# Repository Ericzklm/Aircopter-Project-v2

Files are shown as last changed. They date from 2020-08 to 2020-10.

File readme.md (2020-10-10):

# Aircopter Project

This project was done in association with the IEEE Student Branch on the UCLA campus.
This is the second iteration of the project. Due to the 2020 global pandemic, this
project was cut short for the 2019-2020 academic year and will resume in the 2020-
2021 academic year.

The goal of the project was to: 1. Design and assemble a custom PCB for a drone,
2. Write a program to hover the drone, then fly the drone. Because of the nature
of the project, the PCB was required to be small and compact (meaning SMD soldering
was needed) and the program needed to be quick and responsive.

#### Note: 

This version of the project was cut short due to the 2020 pandemic. The code was still
written and the board was still designed and printed but we were not able to assemble
and solder the final product because we were then living off-campus and all campus
activities we're mandated to be put on hold.

### Hardware Selection Choices:

**MCU**: The main chip is the model STM32F405. This was chosen for its ideal balance
between size and functionality. It is able to support all the needed sensors and
motor drivers for our drone and can be powered by a 3.3v supply which closely
matches the 3.7v of standard drone batteries (3.7v is stepped down to 3.3 using
a voltage regulator). Additionally, this chip was more ideal than other chips of
similar style because it handles floating point calculations better which allows
for simplicity and efficiency when writing the program.

**Voltage Regulator**: The voltage regulator used is the LTC3246MPMSE from Linear 
Technology. This component was chosen since it is a buck boost regulator with
the ability to step down or step up voltage as we need in this application. This
component is larger, more expensive, and more complex than the regulator used in
the first iteration but it accomplishes the same purpose while being much easier
to solder onto the board (no heat guns required).

**Wireless Module**: The wireless module used is the nrf24l01 which is standard, easy
to use, and familiar so we used it in this application since it fits well with the
acclerometer module.

**Accelerometer/Gyroscope**: The module used is the mpu6050 which is standard, easy to
use, and familiar so we used it in this application since it fits well with the
wireless module.

**Oscillator**: We opted for an abracon 25mhz crystal oscillator. The frequency fits 
the range of our operation and takes up a relatively small amount of space on
the PCB. In this iteration, a through-hole component was chosen because it could
be added more compactly without needing large pads on the PCB outside the area of
the oscillator.

**Passive Components**: For the resistors, capacitors, and inductors, we primarily
used parts with the package size 0603 which would fit the board without being
overly difficult to solder. Each piece was checked for its operating voltages as 
well as the operating temperatures to make sure no issues would arise. Additonally,
we tried to get components that were less dependent on external passive components
so we could make the PCB more compact/efficient.

### Hardware Design Choices:

**Motors**: In this design, we opted to place the 4 motor JST connectors along the left
side of the board because this would reduce the amount of "prime-real-estate" occupied
by the motor drivers. Also, we saved a significant amount of space on the PCB by
moving the motor drivers to the backside, under the JST rather than having the drivers
being on the same side (which means we cannot overlap the area occupied by the JSTs).

**Battery**: The JST of the battery is placed directly right of the motors. This is
important since its a central component and that position allows it easy access to
the motors and the rest of the PCB.

**Voltage Regulator**: The voltage regulator is placed below the battery JST, also in a
central position. This is key because we are able to define the 3.7V and 3.3V polygons
without complexity, and therefore reduing bottlenecks. Because the voltage regulator
is dependent on several passive components, it is placed in an open space with the
passive components compactly fit around it, without creating any major bottlenecks.

**Polygons**: Because of the location of the voltage divider, we are able to make an easy
distinction between the 3.3v, 3.7v, motor ground, and general ground planes. Everything
left of the voltage regulator is either the 3.7v or motor ground planes while everything
right is either 3.3v or general ground.

**MCU**: We chose to turn the MCU 45 degrees for a few reasons:
  1. Having the MCU turned actually signficantly reduced the bottlenecks as key 
  components had more direct access to the 3.3v plane and we had less "dead-ends" in 
  the plane. This gave extra space to work in that would not present a threat of 
  bottlenecking.
  2. The traces coming out of the MCU can be shorter and more optimized for the key
  components.
  3. We thought it looked neat!

**Oscillator**: The oscillator is placed as physically close to the MCU as possible with
relatively thick traces in order to prevent that signal from being overly distorted.

**Wireless Module/Accelerometer**: Because these two modules are not raised to the same
level, they can be overlapping on the PCB and not cause any issues. The wireless
module is placed along the right side while the accelerometer is placed along the
bottom because this allows for easy access to the respective connections on the MCU.

**Other items**: This includes the programmer and the reset switch. Since neither of them
are crucial in the operation of the drone, they are place along the top with less
direct connections (meaning the traces and planes for key components are better
optimized). Additionally, this iteration includes a tx and rx connection which will
be useful for debugging.

**Bottlenecks**: For this version, we were able to get away with no major bottlenecks
in the planes thanks to the reduction of passive components, better placements,
and the 45 degree MCU.

**Decoupling Capacitors**: The decoupling capacitors are placed in such a way that they
are close to the components they stabalize. This also helped in reducing bottlenecks
as passive components were not cutting up the planes

### Possible Improvements:

Some components are not optimally placed meaning the traces are not direct. This can
be solved by either tweaking the placement or choosing different compatible pins on
the MCU. Also the placement of the motors and battery mean that the lower motors are
further away from the power source, meaning potentially higher noise. Furthermore,
adding some LEDs would be useful for debugging (we have the room to do so).

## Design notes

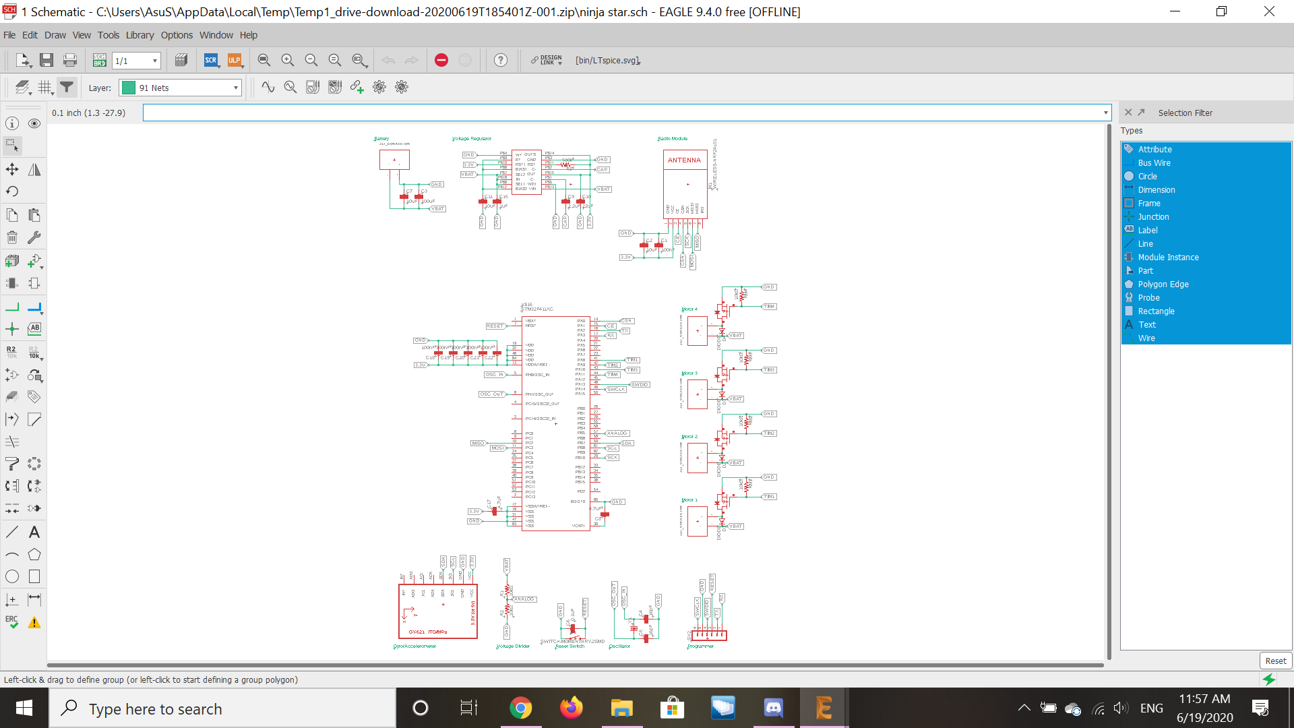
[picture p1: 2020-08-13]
Hardware/Schematic1.png

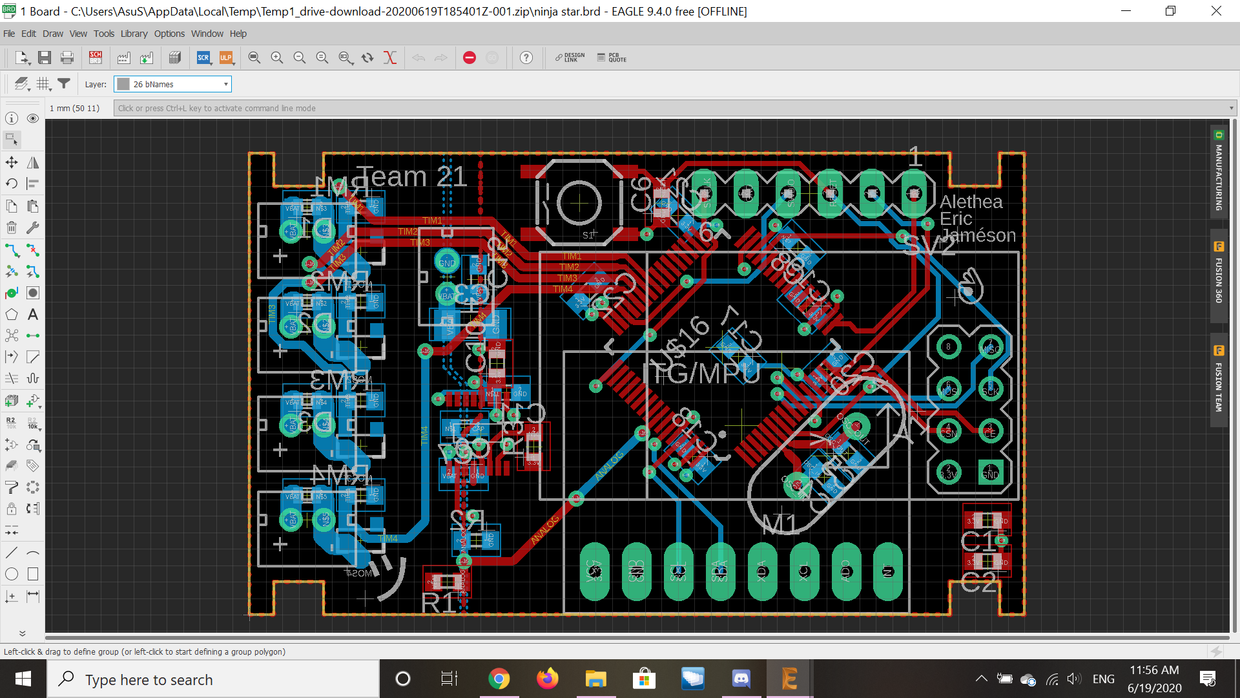
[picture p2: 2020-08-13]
Hardware/PCB2.png

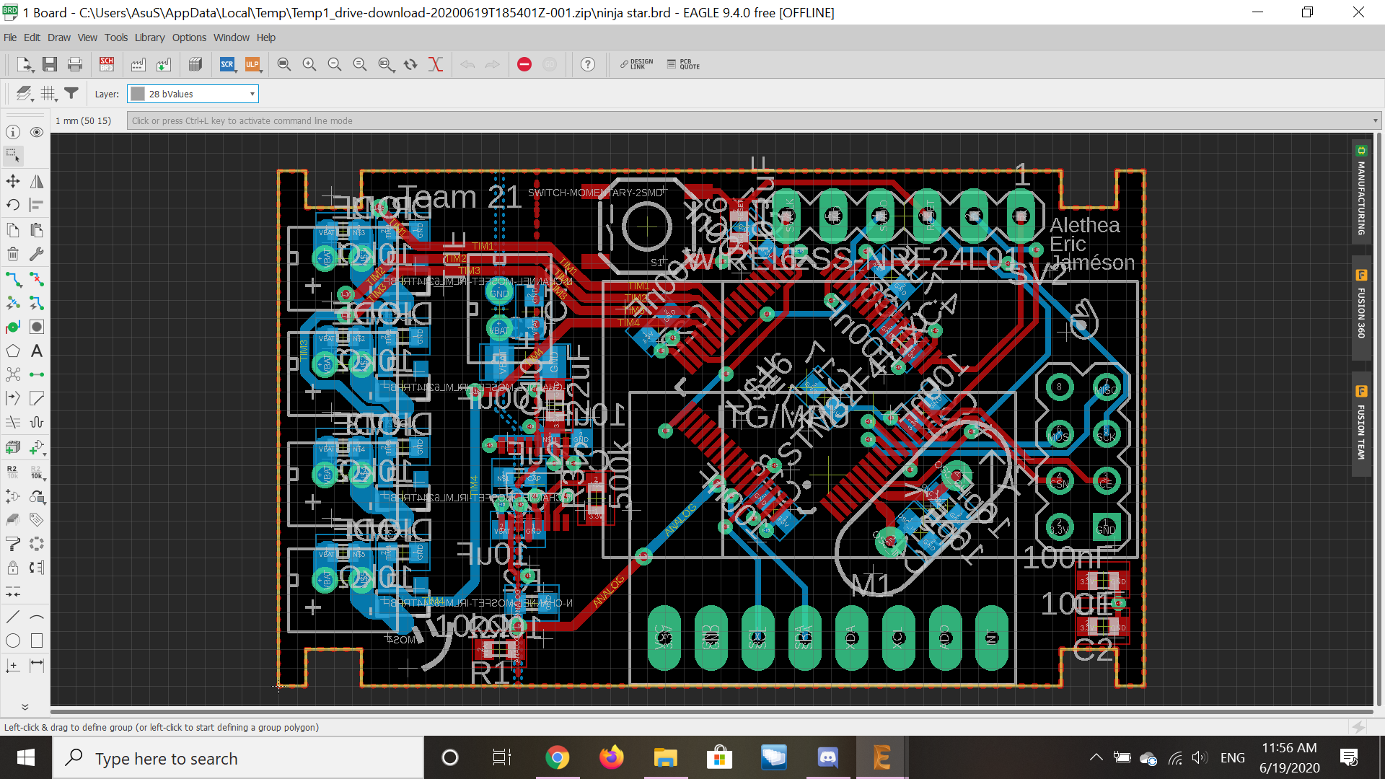
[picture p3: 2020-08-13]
Hardware/PCB4.png

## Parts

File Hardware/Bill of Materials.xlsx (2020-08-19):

Vendor | Vendor Part # | Manufacturer | Part # | Package | Description | Quantity | Unit Price | 65.65 | Link | Datasheet
Mouser | 511-STM32F411CEU6TR | STMicroelectronics | STM32F411CEU6TR | yes | ARM Microcontrollers - MCU High-performance access line, ARM Cortex-M4 core with DSP and FPU, 512 Kbytes Flash, 100 MHz CPU, ART Accelerator | 1 | $5.56 | $5.56 | https://www.mouser.com/ProductDetail/STMicroelectronics/STM32F411CEU6TR | https://www.mouser.com/datasheet/2/389/stm32f411ce-956237.pdf
Mouser | LTC3246MPMSE#PBF | Analog Devices/Linear Technology | TPS63805YFFR | DSBGA-15 | Voltage Regulator | 1 | $15.00 | $15.00 | https://www.mouser.com/ProductDetail/Analog-Devices-Linear-Technology/LTC3246MPMSEPBF | https://www.mouser.com/datasheet/2/609/3246fa-1275517.pdf
Digi-Key | 535-13438-1-ND | Ablacon LC | ABLS2-25.000MHZ-2X-FT | HC-49/US | Crystal Oscillator | 1 | $0.46 | $0.46 | https://www.digikey.com/product-detail/en/abracon-llc/ABLS2-25.000MHZ-2X-FT/535-13438-1-ND/5980114
Digi-Key | GH7585DKR-ND | Grayhill Inc. | 14AP-L1-02-G | Digi-Reel | Pushbutton | 1 | $4.64 | $4.64 | https://www.digikey.com/product-detail/en/grayhill-inc/14AP-L1-02-G/GH7585DKR-ND/5357261
Mouser | 652-CD0603-S01575 | Bourns | CD0603-S01575 | 0603 | Diode | 4 | $0.39 | $1.56 | https://www.mouser.com/ProductDetail/Bourns/CD0603-S01575?qs=FITO%2f%2fQgYDlmbwJLjhqThQ%3d%3d
Mouser | 942-IRLML6244TRPBF | Infineon Technologies | IRLML6244TRPBF | SOT-23-3 | NMOS MOSFET MOSFT 20V 6.3A 21mOhm 2.5V cpbl | 4 | $0.37 | $1.48 | http://www.mouser.com/Search/ProductDetail.aspx | https://www.mouser.com/datasheet/2/196/irlml6244pbf-1228275.pdf
Digi-Key | 490-10525-1-ND | Murata Electronics | GRM31CD80J107ME39L | 1206 | CAP CER 100UF 6.3V X6T 1206 | 1 | $0.76 | $0.76 | https://www.digikey.com/product-detail/en/murata-electronics/GRM31CD80J107ME39L/490-10525-1-ND/5026461 | https://search.murata.co.jp/Ceramy/image/img/A01X/G101/ENG/GRM31CD80J107ME39-01.pdf
Digi-Key | 490-12538-1-ND | Murata Electronics | GRM188R60J106KE47D | 0603 | CAP CER 10UF 6.3V X5R 0603 | 3 | $0.19 | $0.57 | https://www.digikey.com/product-detail/en/murata-electronics/GRM188R60J106KE47D/490-12538-1-ND/5797528 | https://search.murata.co.jp/Ceramy/image/img/A01X/G101/ENG/GRM188R60J106KE47-02.pdf
Digi-Key | 490-12738-1-ND | Murata Electronics | GRM188R61E225MA12D | 0603 | CAP CER 2.2UF 25V X5R 0603 | 1 | $0.16 | $0.16 | https://www.digikey.com/product-detail/en/murata-electronics/GRM188R61E225MA12D/490-12738-1-ND/5797707 | https://search.murata.co.jp/Ceramy/image/img/A01X/G101/ENG/GRM188R61E225MA12-01.pdf
Digi-Key | CL10F104ZO8NNNC | Samsung Electro-Mechanics | 1276-1258-1-ND | 0603 | CAP CER 0.1UF 16V Y5V 0603 | 7 | $0.10 | $0.70 | https://www.digikey.com/product-detail/en/samsung-electro-mechanics/CL10F104ZO8NNNC/1276-1258-1-ND/3889344 | http://www.samsungsem.com/kr/support/product-search/mlcc/CL10F104ZO8NNNC.jsp
Digi-Key | 1276-2204-1-ND | Samsung Electro-Mechanics | CL10C160JB8NNNC | 0603 | CAP CER 16PF 50V C0G/NP0 0603 | 2 | $0.10 | $0.20 | https://www.digikey.com/product-detail/en/samsung-electro-mechanics/CL10C160JB8NNNC/1276-2204-1-ND/3890290 | http://www.samsungsem.com/kr/support/product-search/mlcc/__icsFiles/afieldfile/2018/06/11/CL10C160JB8NNNC.pdf
Digi-Key | 1276-6524-1-ND | Samsung Electro-Mechanics (http://www.samsungsem.com/global/index.jsp) | CL10B105MO8NNWC | 0603 | CAP CER 1UF 16V X7R 0603 | 1 | $0.10 | $0.10 | https://www.digikey.com/product-detail/en/samsung-electro-mechanics/CL10B105MO8NNWC/1276-6524-1-ND/5961383 | http://www.samsungsem.com/kr/support/product-search/mlcc/__icsFiles/afieldfile/2018/07/24/CL10B105MO8NNWC.pdf
Digi-Key | 1276-2868-1-ND | Samsung Electro-Mechanics | CL10A226MQ8NRNE | 0603 | CAP CER 22UF 6.3V X5R 0603 | 1 | $0.34 | $0.34 | https://www.digikey.com/product-detail/en/samsung-electro-mechanics/CL10A226MQ8NRNE/1276-2868-1-ND/3890954 | http://www.samsungsem.com/kr/support/product-search/mlcc/__icsFiles/afieldfile/2018/06/20/CL10A226MQ8NRNE.pdf
Digi-Key | 311-1820-1-ND | Yageo | CC0603MRX5R6BB475 | 0603 | CAP CER 4.7UF 10V X5R 0603 | 2 | $0.21 | $0.42 | https://www.digikey.com/product-detail/en/yageo/CC0603MRX5R6BB475/311-1820-1-ND/5195722 | https://www.yageo.com/upload/media/product/productsearch/datasheet/mlcc/UPY-GPHC_X5R_4V-to-50V_25.pdf
Digi-Key | 311-10KGRCT-ND | Yageo | RC0603JR-0710KL | 0603 | RES SMD 10K OHM 5% 1/10W 0603 | 6 | $0.10 | $0.60 | https://www.digikey.com/product-detail/en/yageo/RC0603JR-0710KL/311-10KGRCT-ND/729647 | https://www.yageo.com/upload/media/product/productsearch/datasheet/rchip/PYu-RC_Group_51_RoHS_L_10.pdf
Digi-Key | 749-1661-1-ND | Vishay Beyschlag | MCT06030C4993FP500 | 0603 | RES SMD 499K OHM 1% 1/8W 0603 | 1 | $0.17 | $0.17 | https://www.digikey.com/product-detail/en/vishay-beyschlag/MCT06030C4993FP500/749-1661-1-ND/7347969 | http://www.vishay.com/docs/28705/mcx0x0xpro.pdf
 |  |  |  |  |  |  |  | 0
 |  |  |  |  |  |  |  | 0
 |  |  |  |  |  |  |  | 0
 |  |  |  |  |  |  |  | 0
 |  |  |  |  |  |  |  | 0
 |  |  |  |  |  |  |  | 0
 |  |  |  |  |  |  |  | 0
 |  |  |  |  |  |  |  | 0
 |  |  |  |  |  |  |  | 0
 |  |  |  |  |  |  |  | 0

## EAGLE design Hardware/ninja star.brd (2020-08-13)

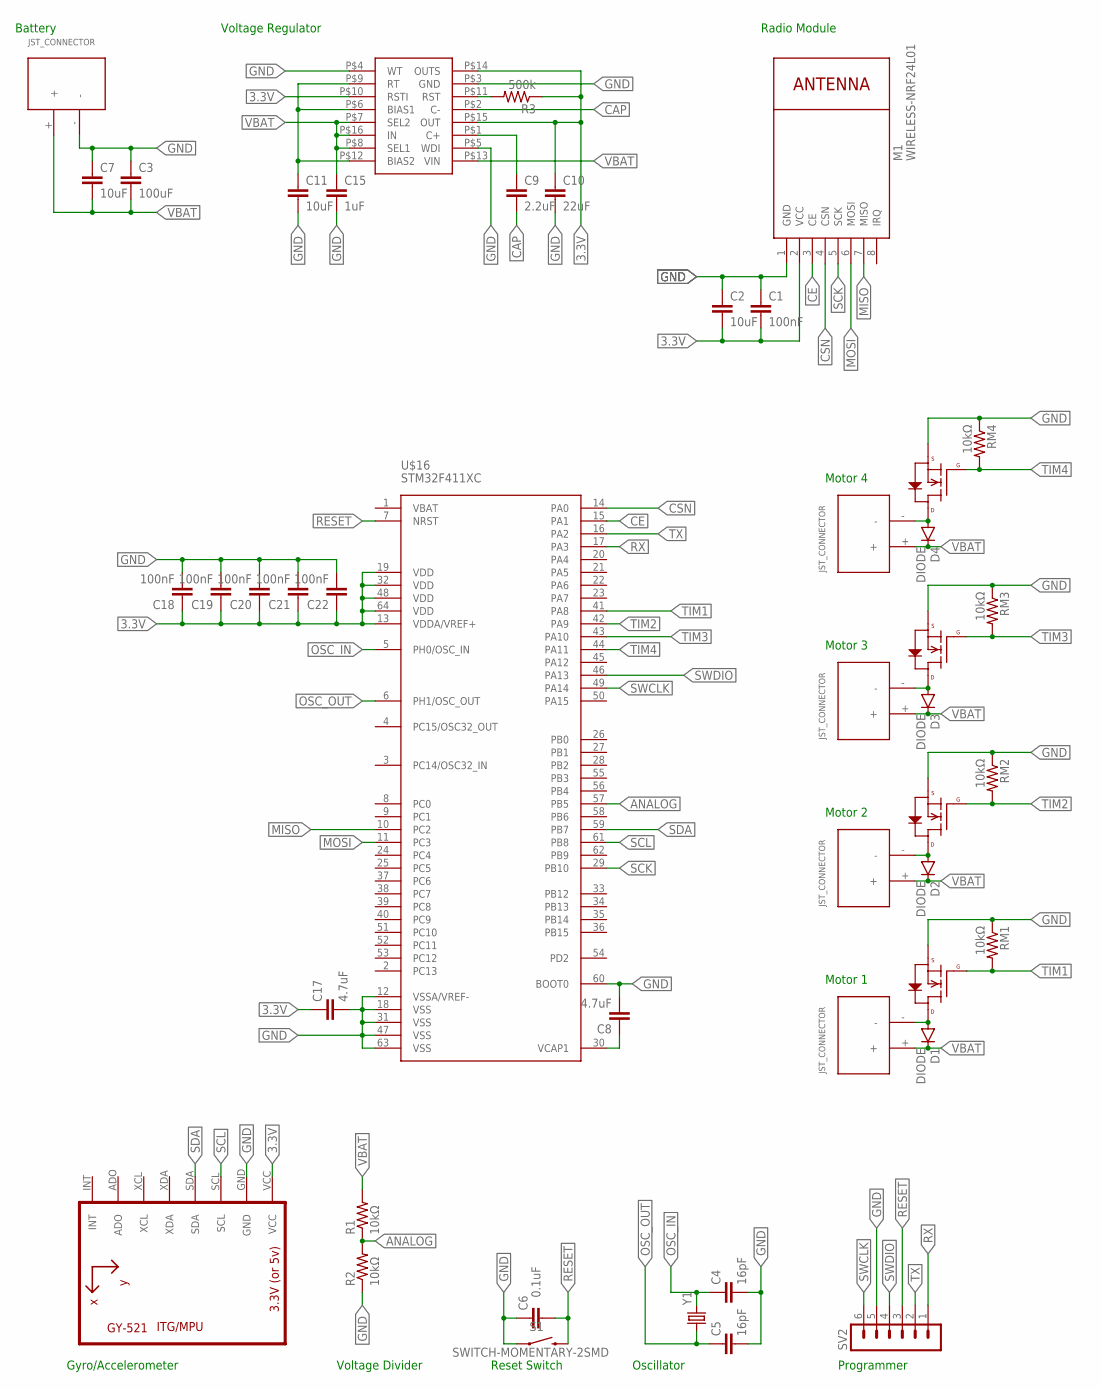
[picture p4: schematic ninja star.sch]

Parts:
C1, C18, C19, C20, C21, C22: 100nF; C0603
C2, C7, C11: 10uF; C0603
C3: 100uF; C1206
C4, C5: 16pF; C0603
C6: 0.1uF; C0603
C8, C17: 4.7uF; C0603
C9: 2.2uF; C0603
C10: 22uF; C0603
C15: 1uF; C0603
D1, D2, D3, D4: DIODE; C0603
M1: WIRELESS-NRF24L01
MOS1, MOS2, MOS3, MOS4: N-CHANNEL-MOSFET-IRLML6244TRPBF; SOT23-3
MOTOR1, MOTOR2, MOTOR3, MOTOR4: JST_CONNECTOR_FEMALE
R1, R2: 10kΩ; R0603
R3: 500k; R0603
RM1, RM2, RM3, RM4: 10kΩ; R0603
S1: SWITCH-MOMENTARY-2SMD; TACTILE-SWITCH-SMD
SV2: MA06-1
U1: GY-521MPU6050; GY-521
U$7: JST_CONNECTOR_FEMALE
U$12: VR-LTC3246; MSOP-16
U$16: STM32F411XC; LQFP64
Y1: CRYSTALHC49US; HC49US

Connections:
3.3V: C1.2, C2.2, C10.1, C17.1, C18.1, C19.1, C20.1, C21.1, C22.1, M1.2 (VCC), R3.1, U1.VCC, U$12.P$10 (RSTI), U$12.P$14 (OUTS), U$12.P$15 (OUT), U$16.13 (VDDA/VREF+), U$16.19 (VDD), U$16.32 (VDD), U$16.48 (VDD), U$16.64 (VDD)
ANALOG: R1.1, R2.2, U$16.57 (PB5)
CAP: C9.2, U$12.P$2 (C-)
CE: M1.3 (CE), U$16.15 (PA1)
CSN: M1.4 (CSN), U$16.14 (PA0)
GND: C1.1, C2.1, C3.1, C4.2, C5.2, C6.1, C7.1, C8.2, C10.2, C11.2, C15.2, C17.2, C18.2, C19.2, C20.2, C21.2, C22.2, M1.1 (GND), MOS1.2 (S), MOS2.2 (S), MOS3.2 (S), MOS4.2 (S), R2.1, RM1.1, RM2.1, RM3.1, RM4.1, S1.1, SV2.5, U1.GND, U$7.-, U$12.P$3 (GND), U$12.P$4 (WT), U$12.P$5 (WDI), U$16.12 (VSSA/VREF-), U$16.18 (VSS), U$16.31 (VSS), U$16.47 (VSS), U$16.60 (BOOT0), U$16.63 (VSS)
MISO: M1.7 (MISO), U$16.10 (PC2)
MOSI: M1.6 (MOSI), U$16.11 (PC3)
unnamed: C9.1, U$12.P$1 (C+)
unnamed: D2.2 (PPIN), MOS2.3 (D), MOTOR2.-
unnamed: D1.2 (PPIN), MOS1.3 (D), MOTOR1.-
unnamed: D3.2 (PPIN), MOS3.3 (D), MOTOR3.-
unnamed: D4.2 (PPIN), MOS4.3 (D), MOTOR4.-
unnamed: R3.2, U$12.P$11 (RST)
unnamed: C8.1, U$16.30 (VCAP1)
unnamed: C11.1, U$12.P$6 (BIAS1), U$12.P$9 (RT), U$12.P$12 (BIAS2)
OSC_IN: C4.1, U$16.5 (PH0/OSC_IN), Y1.2
OSC_OUT: C5.1, U$16.6 (PH1/OSC_OUT), Y1.1
RESET: C6.2, S1.3 (2), SV2.3, U$16.7 (NRST)
RX: SV2.1, U$16.17 (PA3)
SCK: M1.5 (SCK), U$16.29 (PB10)
SCL: U1.SCL, U$16.61 (PB8)
SDA: U1.SDA, U$16.59 (PB7)
SWCLK: SV2.6, U$16.49 (PA14)
SWDIO: SV2.4, U$16.46 (PA13)
TIM1: MOS1.1 (G), RM1.2, U$16.41 (PA8)
TIM2: MOS2.1 (G), RM2.2, U$16.42 (PA9)
TIM3: MOS3.1 (G), RM3.2, U$16.43 (PA10)
TIM4: MOS4.1 (G), RM4.2, U$16.44 (PA11)
TX: SV2.2, U$16.16 (PA2)
VBAT: C3.2, C7.2, C15.1, D1.1 (GPIN), D2.1 (GPIN), D3.1 (GPIN), D4.1 (GPIN), MOTOR1.+, MOTOR2.+, MOTOR3.+, MOTOR4.+, R1.2, U$7.+, U$12.P$7 (SEL2), U$12.P$8 (SEL1), U$12.P$13 (VIN), U$12.P$16 (IN)

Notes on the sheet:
Battery
Voltage Divider
Voltage Regulator
Radio Module
Motor 4
Motor 3
Motor 2
Motor 1
Gyro/Accelerometer
Reset Switch
Oscillator
Programmer

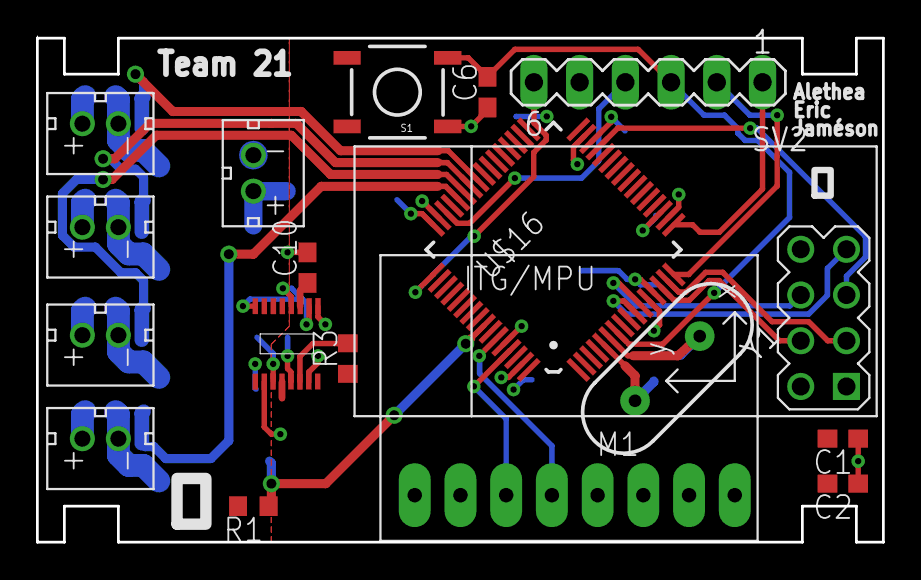
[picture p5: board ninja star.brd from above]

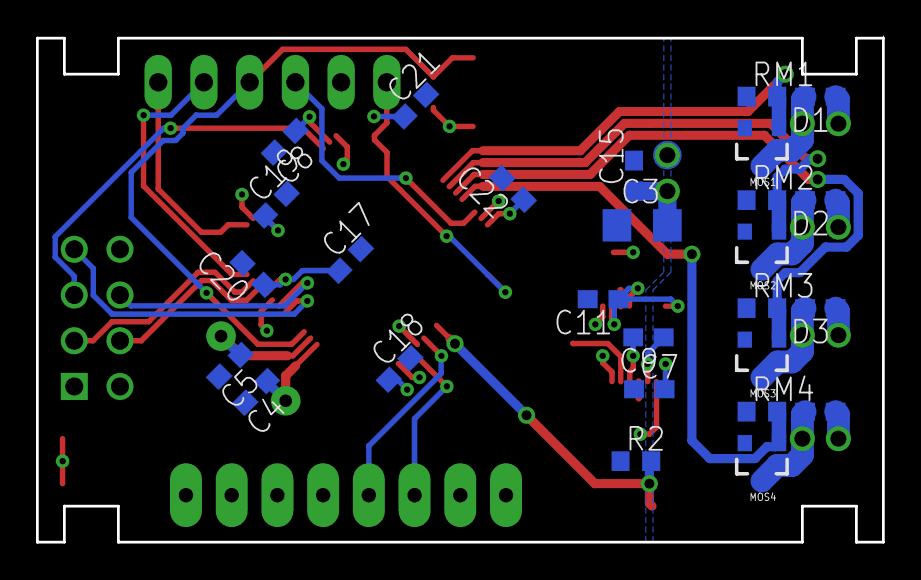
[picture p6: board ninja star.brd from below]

Board: 2 copper layers, 47.0 x 28.0 mm, 45 parts (27 on the bottom side), 31 nets.

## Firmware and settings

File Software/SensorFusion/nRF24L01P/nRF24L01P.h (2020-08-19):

#ifndef __NRF24L01P_H__
#define __NRF24L01P_H__

/**
 * Includes
 */
#include "mbed.h"

/**
 * Defines
 */
#define NRF24L01P_TX_PWR_ZERO_DB         0
#define NRF24L01P_TX_PWR_MINUS_6_DB     -6
#define NRF24L01P_TX_PWR_MINUS_12_DB   -12
#define NRF24L01P_TX_PWR_MINUS_18_DB   -18

#define NRF24L01P_DATARATE_250_KBPS    250
#define NRF24L01P_DATARATE_1_MBPS     1000
#define NRF24L01P_DATARATE_2_MBPS     2000

#define NRF24L01P_CRC_NONE               0
#define NRF24L01P_CRC_8_BIT              8
#define NRF24L01P_CRC_16_BIT            16

#define NRF24L01P_MIN_RF_FREQUENCY    2400
#define NRF24L01P_MAX_RF_FREQUENCY    2525

#define NRF24L01P_PIPE_P0                0
#define NRF24L01P_PIPE_P1                1
#define NRF24L01P_PIPE_P2                2
#define NRF24L01P_PIPE_P3                3
#define NRF24L01P_PIPE_P4                4
#define NRF24L01P_PIPE_P5                5

/**
* Default setup for the nRF24L01+, based on the Sparkfun "Nordic Serial Interface Board"
*  for evaluation (http://www.sparkfun.com/products/9019)
*/
#define DEFAULT_NRF24L01P_ADDRESS       ((unsigned long long) 0xE7E7E7E7E7 )
#define DEFAULT_NRF24L01P_ADDRESS_WIDTH  5
#define DEFAULT_NRF24L01P_CRC            NRF24L01P_CRC_8_BIT
#define DEFAULT_NRF24L01P_RF_FREQUENCY  (NRF24L01P_MIN_RF_FREQUENCY + 2)
#define DEFAULT_NRF24L01P_DATARATE       NRF24L01P_DATARATE_1_MBPS
#define DEFAULT_NRF24L01P_TX_PWR         NRF24L01P_TX_PWR_ZERO_DB
#define DEFAULT_NRF24L01P_TRANSFER_SIZE  4

/**
 * nRF24L01+ Single Chip 2.4GHz Transceiver from Nordic Semiconductor.
 */
class nRF24L01P {

public:

    /**
     * Constructor.
     *
     * @param mosi mbed pin to use for MOSI line of SPI interface.
     * @param miso mbed pin to use for MISO line of SPI interface.
     * @param sck mbed pin to use for SCK line of SPI interface.
     * @param csn mbed pin to use for not chip select line of SPI interface.
     * @param ce mbed pin to use for the chip line.
     * @param irq mbed pin to use for the interrupt request line.
     */
    nRF24L01P(PinName mosi, PinName miso, PinName sck, PinName csn, PinName ce, PinName irq = NC);

    /**
     * Set the RF frequency.
     *
     * @param frequency the frequency of RF transmission in MHz (2400..2525).
     */
    void setRfFrequency(int frequency = DEFAULT_NRF24L01P_RF_FREQUENCY);

    /**
     * Get the RF frequency.
     *
     * @return the frequency of RF transmission in MHz (2400..2525).
     */
    int getRfFrequency(void);

    /**
     * Set the RF output power.
     *
     * @param power the RF output power in dBm (0, -6, -12 or -18).
     */
    void setRfOutputPower(int power = DEFAULT_NRF24L01P_TX_PWR);

    /**
     * Get the RF output power.
     *
     * @return the RF output power in dBm (0, -6, -12 or -18).
     */
    int getRfOutputPower(void);

    /**
     * Set the Air data rate.
     *
     * @param rate the air data rate in kbps (250, 1M or 2M).
     */
    void setAirDataRate(int rate = DEFAULT_NRF24L01P_DATARATE);

    /**
     * Get the Air data rate.
     *
     * @return the air data rate in kbps (250, 1M or 2M).
     */
    int getAirDataRate(void);

    /**
     * Set the CRC width.
     *
     * @param width the number of bits for the CRC (0, 8 or 16).
     */
    void setCrcWidth(int width = DEFAULT_NRF24L01P_CRC);

    /**
     * Get the CRC width.
     *
     * @return the number of bits for the CRC (0, 8 or 16).
     */
    int getCrcWidth(void);

    /**
     * Set the Receive address.
     *
     * @param address address associated with the particular pipe
     * @param width width of the address in bytes (3..5)
     * @param pipe pipe to associate the address with (0..5, default 0)
     *
     * Note that Pipes 0 & 1 have 3, 4 or 5 byte addresses,
     *  while Pipes 2..5 only use the lowest byte (bits 7..0) of the
     *  address provided here, and use 2, 3 or 4 bytes from Pipe 1's address.
     *  The width parameter is ignored for Pipes 2..5.
     */
    void setRxAddress(unsigned long long address = DEFAULT_NRF24L01P_ADDRESS, int width = DEFAULT_NRF24L01P_ADDRESS_WIDTH, int pipe = NRF24L01P_PIPE_P0);

    void setRxAddress(unsigned long msb_address, unsigned long lsb_address, int width, int pipe = NRF24L01P_PIPE_P0);

    /**
     * Set the Transmit address.
     *
     * @param address address for transmission
     * @param width width of the address in bytes (3..5)
     *
     * Note that the address width is shared with the Receive pipes,
     *  so a change to that address width affect transmissions.
     */
    void setTxAddress(unsigned long long address = DEFAULT_NRF24L01P_ADDRESS, int width = DEFAULT_NRF24L01P_ADDRESS_WIDTH);

    void setTxAddress(unsigned long msb_address, unsigned long lsb_address, int width);

    /**
     * Get the Receive address.
     *
     * @param pipe pipe to get the address from (0..5, default 0)
     * @return the address associated with the particular pipe
     */
    unsigned long long getRxAddress(int pipe = NRF24L01P_PIPE_P0);

    /**
     * Get the Transmit address.
     *
     * @return address address for transmission
     */
    unsigned long long getTxAddress(void);

    /**
     * Set the transfer size.
     *
     * @param size the size of the transfer, in bytes (1..32)
     * @param pipe pipe for the transfer (0..5, default 0)
     */
    void setTransferSize(int size = DEFAULT_NRF24L01P_TRANSFER_SIZE, int pipe = NRF24L01P_PIPE_P0);

    /**
     * Get the transfer size.
     *
     * @return the size of the transfer, in bytes (1..32).
     */
    int getTransferSize(int pipe = NRF24L01P_PIPE_P0);


    /**
     * Get the RPD (Received Power Detector) state.
     *
     * @return true if the received power exceeded -64dBm
     */
    bool getRPD(void);

    /**
     * Put the nRF24L01+ into Receive mode
     */
    void setReceiveMode(void);

    /**
     * Put the nRF24L01+ into Transmit mode
     */
    void setTransmitMode(void);

    /**
     * Power up the nRF24L01+ into Standby mode
     */
    void powerUp(void);

    /**
     * Power down the nRF24L01+ into Power Down mode
     */
    void powerDown(void);

    /**
     * Enable the nRF24L01+ to Receive or Transmit (using the CE pin)
     */
    void enable(void);

    /**
     * Disable the nRF24L01+ to Receive or Transmit (using the CE pin)
     */
    void disable(void);

    /**
     * Transmit data
     *
     * @param pipe is ignored (included for consistency with file write routine)
     * @param data pointer to an array of bytes to write
     * @param count the number of bytes to send (1..32)
     * @return the number of bytes actually written, or -1 for an error
     */
    int write(int pipe, char *data, int count);
    
    /**
     * Receive data
     *
     * @param pipe the receive pipe to get data from
     * @param data pointer to an array of bytes to store the received data
     * @param count the number of bytes to receive (1..32)
     * @return the number of bytes actually received, 0 if none are received, or -1 for an error
     */
    int read(int pipe, char *data, int count);

    /**
     * Determine if there is data available to read
     *
     * @param pipe the receive pipe to check for data
     * @return true if the is data waiting in the given pipe
     */
    bool readable(int pipe = NRF24L01P_PIPE_P0);

    /**
     * Disable all receive pipes
     *
     * Note: receive pipes are enabled when their address is set.
     */
    void disableAllRxPipes(void);
    
    /**
     * Disable AutoAcknowledge function
     */
    void disableAutoAcknowledge(void);
    
    /**
     * Enable AutoAcknowledge function
     *
     * @param pipe the receive pipe
     */
    void enableAutoAcknowledge(int pipe = NRF24L01P_PIPE_P0);
    
    /**
     * Disable AutoRetransmit function
     */
    void disableAutoRetransmit(void);
    
    /**
     * Enable AutoRetransmit function
     *
     * @param delay the delay between restransmits, in uS (250uS..4000uS)
     * @param count number of retransmits before generating an error (1..15)
     */
    void enableAutoRetransmit(int delay, int count);

private:

    /**
     * Get the contents of an addressable register.
     *
     * @param regAddress address of the register
     * @return the contents of the register
     */
    int getRegister(int regAddress);

    /**
     * Set the contents of an addressable register.
     *
     * @param regAddress address of the register
     * @param regData data to write to the register
     */
    void setRegister(int regAddress, int regData);

    /**
     * Get the contents of the status register.
     *
     * @return the contents of the status register
     */
    int getStatusRegister(void);

    SPI         spi_;
    DigitalOut  nCS_;
    DigitalOut  ce_;
    InterruptIn nIRQ_;

    int mode;

};

#endif /* __NRF24L01P_H__ */

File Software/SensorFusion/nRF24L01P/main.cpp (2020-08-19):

#include "mbed.h"
#include "sensor_fusion.h"
#include "quaternion.h"
#include "millis.h"



MPU6050 MPU(D4,D5);
Serial pc(USBTX, USBRX); //create a Serial object
Timer timer;

int main() {
    MPU.start();
    timer.start();
    pc.baud(115200);
    float t;
    float mag;
    float pi = 3.14159265358979;
    int i=0;
    float sumgx,sumgy,sumgz,sumax,sumay,sumaz;
    float biasgx,biasgy,biasgz,biasax,biasay,biasaz;
    float gx,gy,gz,ax,ay,az;
    
    vector n;
    n.x=0;
    n.y=0;
    n.z=1;
    
    vector pointv;
    pointv.x=0;
    pointv.y=0;
    pointv.z=1;
    
    
    while(i<=19) 
    {
            
        if (MPU.data_ready() == 1) 
        {
            MPU.read_raw(&gx,&gy,&gz,&ax,&ay,&az);
            sumgx+=gx;
            sumgy+=gy;
            sumgz+=gz;
            sumax+=ax;
            sumay+=ay;
            sumaz+=az;
        } 
    i++;
    }
                biasgx=sumgx/20;
                biasgy=sumgy/20;
                biasgz=sumgz/20;
                biasax=sumax/20;
                biasay=sumay/20;
                biasaz=sumaz/20;        
               
    while(i<=100)
    {
        if (MPU.data_ready() == 1) 
        {
            MPU.read_raw(&gx,&gy,&gz,&ax,&ay,&az);
            gx=gx-biasgx;
            gy=gy-biasgy;
            gz=gz-biasgz;
            ax=ax-biasax;
            ay=ay-biasay;
            az=az-biasaz +16384;
               /*
                pc.printf("%f\n\r", gx);
                pc.printf("%f\n\r", gy);
                pc.printf("%f\n\r", gz);
                pc.printf("%f\n\r", ax);
                pc.printf("%f\n\r", ay);
                pc.printf("%f\n\r", az);*/
                
        }   
            //pc.printf("%f \r\n", ax);
            vector initial; 
            initial.x = ax;
            initial.y = ay;
            initial.z = az;
            vector unit;
            vector_normalize(&initial,&unit);
//checkpoint 3
               

            
            vector v;
            t=(timer.read_ms())/1000.0;
            timer.reset();
            v.x= gx;
            v.y= gy;
            v.z= gz;

            quaternion q;
            vector unitv;
            vector compfilter;
            vector alphainitial;
            vector alphanrotate;
            vector nrotate;
            vector pointvunit;
           
            mag = -((vector_normalize(&v,&unitv))/(2952.0))*(t*pi);
            quaternion_create(&unitv, mag, &q);
            quaternion_rotate(&pointv,&q, &pointv);
            vector_normalize(&pointv,&pointvunit);
//checkpoint 4

            
            //n = normalize(𝛼a + (1 - 𝛼)rotate(n))
            vector_multiply(&initial,.1,&alphainitial);
            quaternion_rotate(&n,&q,&nrotate);
            vector_multiply(&nrotate,.9,&alphanrotate);
            vector_add(&alphainitial,&alphanrotate, &compfilter);
            vector_normalize(&compfilter, &n);
//checkpoint 5
            
            pc.printf("%f %f %f %f %f %f %f %f %f\r\n", unit.x,unit.y,unit.z,pointvunit.x,pointvunit.y,pointvunit.z,n.x,n.y,n.z);
            wait_ms(100);

            
    }
        i++;
        timer.reset(); 




}

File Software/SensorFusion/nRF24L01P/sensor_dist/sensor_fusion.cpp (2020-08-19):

/* 
 * @author: Natasha Sarkar, 2018
 */

#include "mbed.h"
#include "sensor_fusion.h"
 
MPU6050::MPU6050(PinName sda, PinName scl): i2c_object(sda, scl) {
    i2c_object.frequency(400000);
}
 
void MPU6050::start(void) {
    write_reg(ADDRESS, PWR_MGMT_1, 0x00);
    write_reg(ADDRESS, GYRO_CONFIG, 0x03 << 3);
    write_reg(ADDRESS, ACCEL_CONFIG, 0x00);
    write_reg(ADDRESS, CONFIG, 0x00);
}
 
bool MPU6050::read_raw(float *gx, float *gy, float *gz, float *ax, float *ay, float *az) {
    char raw_gyro[6];
    char raw_accel[6];
    if (read_reg(ADDRESS, GYRO_X, raw_gyro, 6)) {
        read_reg(ADDRESS, ACCEL_X, raw_accel, 6);
        *gx = float(short(raw_gyro[0] << 8 | raw_gyro[1]));
        *gy = float(short(raw_gyro[2] << 8 | raw_gyro[3]));
        *gz = float(short(raw_gyro[4] << 8 | raw_gyro[5]));
        *ax = float(short(raw_accel[0] << 8 | raw_accel[1]));
        *ay = float(short(raw_accel[2] << 8 | raw_accel[3]));
        *az = float(short(raw_accel[4] << 8 | raw_accel[5]));
        return true;
    }
    return false;
}

bool MPU6050::data_ready(void) {
    char int_status;
    read_reg(ADDRESS, INT_STATUS, &int_status, 1);
    return int_status & 1;
}

bool MPU6050::write_reg(int addr, char reg, char buf) {
    char data[2] = {reg, buf};
    return MPU6050::i2c_object.write(addr, data, 2) == 0;
}
 
bool MPU6050::read_reg(int addr, char reg, char *buf, int length) {
    return i2c_object.write(addr, &reg, 1, true) == 0 && 
           i2c_object.read(addr, buf, length) == 0;
}

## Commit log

2020-08-13 Added Hardware Changes and Files.
    [Bill of Materials.xlsx, ninja star.brd, ninja star.sch]
2020-08-19 Bug Fixes, Organization, and Documentation.
    [Bill of Materials.xlsx, ninja star.brd, ninja star.sch]
